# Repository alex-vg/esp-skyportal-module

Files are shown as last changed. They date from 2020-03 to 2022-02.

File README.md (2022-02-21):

## How to make your own ESPSkyPortalModule (a cheap Celestron SkyPortal Wifi-Module alternative)

This little project was inspired by finding a cheaper alternative to the Celestron SkyPortal Wifi Module for NexStar Goto Mounts. With 150€ for such a simple device, it would be crazy not to try and do it ourself. At the end tho, I did not expect that many problems with getting it to communicate correctly, but now it all works fine and I want to share it with you.

If you like this project, you can buy me a beer. Cheers!



### needed stuff:
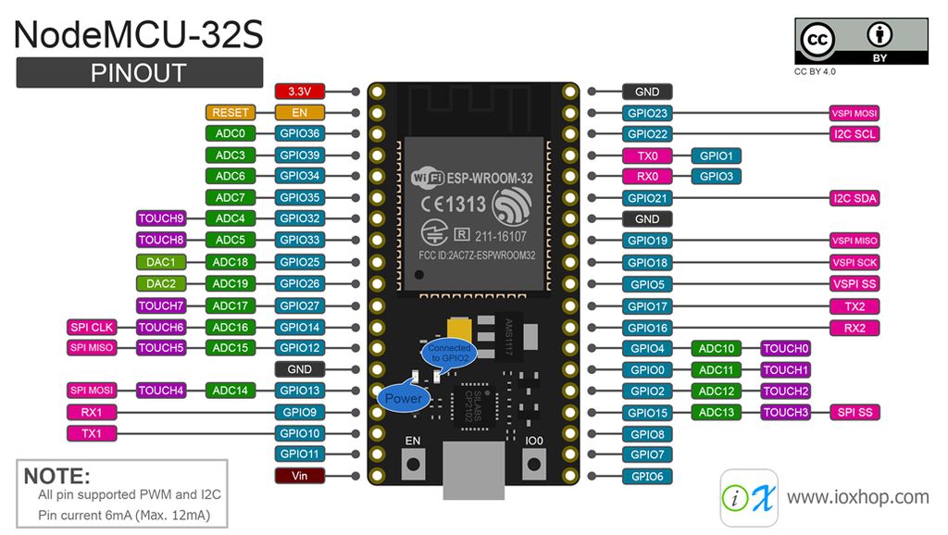
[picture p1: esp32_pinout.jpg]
esp32 pinout

- ESP32, the cheap "NodeMCU32" (see pinout to get the one I used, there are diffrent versions idk if every version works fine)
- 50k-100k resistor (i used exactly 93k ohm, ~2x46k)
- a diode (1N4001, but any other should be ok)
- a small step down converter, to get 5V out of 12V
- RJ12 cable to plug in the device
- (optional) a case or box to protect it

### Pins we need to connect from the 6-pin RJ12 cable:
- PIN3 green - 12V (to step-down module)
- PIN4 yellow - data (to TXPIN, RXPIN and 3.3v)
- PIN5 pink - ground (to every gnd)
- PIN6 gray/black - select (to SELPIN)

Connect the TX pin to the data pin via the diode. TX will just pull the line down, and we need to prevent a high-override. (If Nexstar Device pulls down, this TX output could keep the line high.)
Connect RX Pin directly to the data pin.
```
3.3v --[100k]--+
TXPIN ----<|---+--Data Pin 
RXPIN ---------+
```
Connect a 40k-50k resistor between 3.3v and Data Pin. (a weak pullup, since TX can't pull up anymore and the signal would rise slowly on TX Down -> TX High transition)

Connect the SELPIN directly to the select pin on the RJ12.

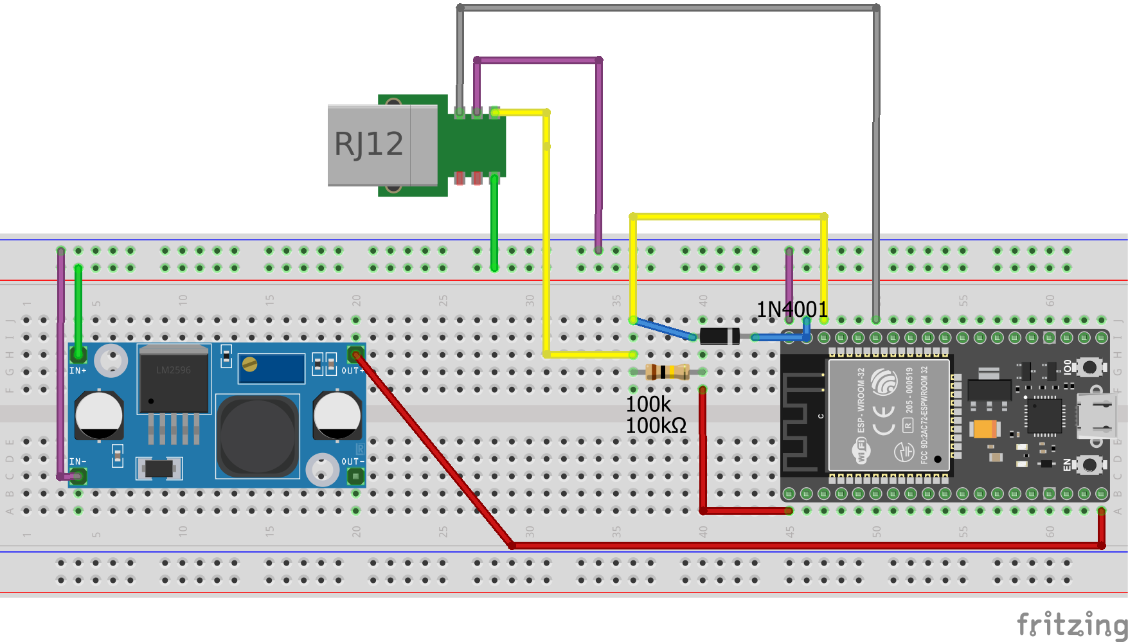
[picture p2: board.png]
board


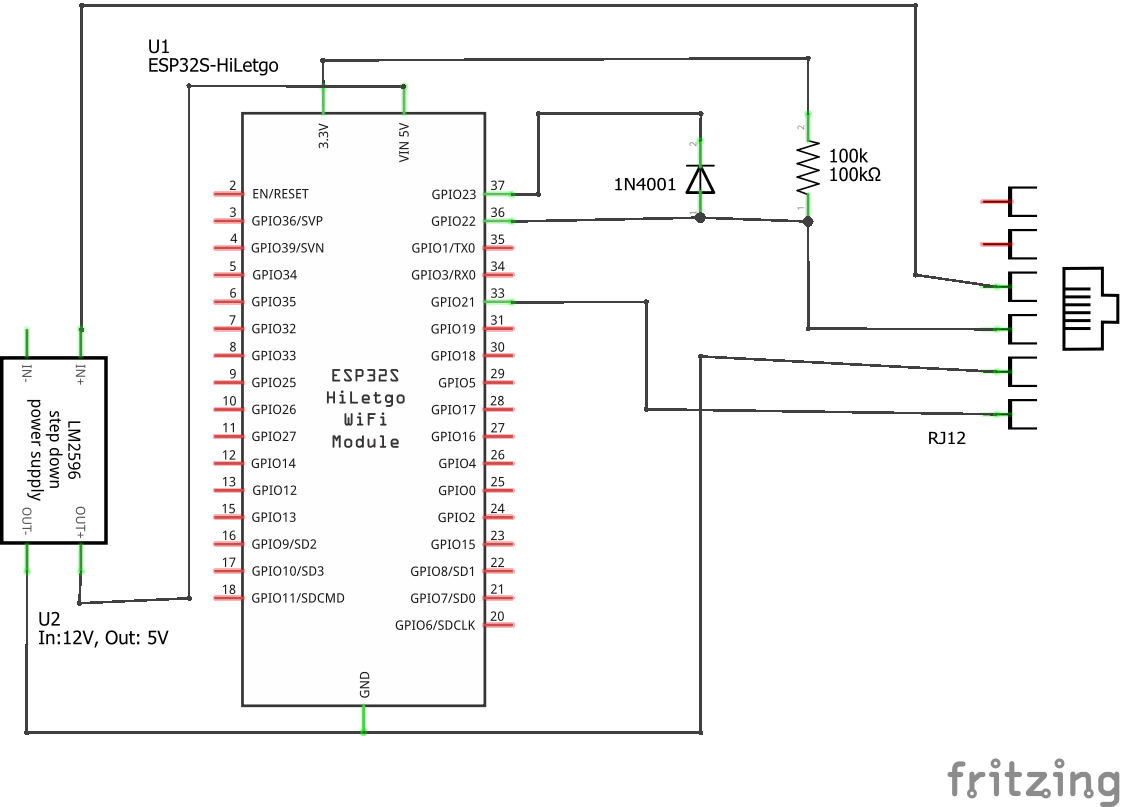
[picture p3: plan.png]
plan


### 5V = 3.3V ?
And yes, we connect our 3.3V IO pins from ESP32 to a potential 5V line. I tried some 3V/5V converters but there are always problems in level shifting.
So the signal from the NexStar is not readable anymore. Then I realized that the Handcontrol is sending at 5V, but the mainboard is responding with a 3.3V level.
The guys from Celestron directly connected 5V and 3.3V logic. Not a good start, but I guessd we could do the same for this project - and it all worked fine.
The only thing that could get grilled is our ESP32, which is cheap.
(But I would still suggest to avoid this in professional product development!)

The device advertises itself via broadcasting its firmware version and mac address.
The control software connects to a tcp port 2000 on ip 1.2.3.4 if the device is in AP mode.
There is a special protocol, but all we need to do is to figure out when a message is complete, since the length of a message can vary. 
After we got a message in the tcp stream, we proxy it to the serial interface and vice versa.

### ToDo-List

- [x] implement Celestron AUX proxy
- [x] implement access-point mode
- [ ] get wifi config with wifi in client-mode working

The original dongle can connect to an existing wifi, after it is configured via the software.
For this connection the software connects to a sort of telnet interface on port 3000.

This is a communication that I sniffed while configuring the original module, to connect to my Wifi with the name Special"Character"WifiName (NX is a message from NexStar, PC is my PC, [0x0d 0x0a] is just a next-line-character):
```
NX:"> "
PC:"get wlan.ssid[0x0d 0x0a]"
NX:Wifiname[0x0d 0x0a]
NX:"> "
...now there are more commands like the one above...
PC:"set wlan.ssid "Special"Character"WifiName"[0x0d 0x0a]"
NX:"Set OK[0x0d 0x0a]"
NX:"> "
...now there are more commands like the one above...
PC:"save[0x0d 0x0a]"
NX:"Success[0x0d 0x0a]"
NX:"> "
```
This is part of ZentriOS (by Silicon Labs) and is indeed a full telnet server with much more functionality.

Commands needed (set and get):

```
set wlan.ssid "ssidname"
set wlan.passkey "mypassword123"
set wlan.static.netmask 0.0.0.0
set wlan.static.ip 0.0.0.0
set wlan.static.gateway 0.0.0.0
set wlan.dhcp.enabled 1
```
Currently I'm not into developing a fake telnet server and since for me there is no need to use an existing wifi, my digitalRead(motivation) returns LOW. But if someone needs this, feel free to contact me.

The ESP32 is available in a "secured" network with the name Celestron-F7F and the password 123456789, which can be changed in the code.

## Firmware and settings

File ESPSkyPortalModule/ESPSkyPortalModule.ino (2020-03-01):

// https://github.com/espressif/arduino-esp32/tree/master/libraries/WiFi/src

//#define DEBUG
//#define DEBUG_INOUT
//#define DEBUG_CRAZY

#include <WiFi.h>
#include <WiFiUdp.h>

#define RXPIN 22
#define TXPIN 23
#define SELPIN 21
#define LEDPIN 2

// Replace with your network credentials
const char* ssid     = "Celestron-F7F";
const char* password = "123456789";

// advertisement over udp. interestingly, the mac advertised starts with 4C, but the actual mac is starting with 4E.
// the end "0F:80" is (0x0F, 0x7F) +1 because WiFi.h uses a diffrent MAC (mac+1) for the server than for wifi advertisment.
const char* advertisment = "{\"mac\":\"4C:55:CC:1A:0F:80\",\"version\":\"ZENTRI-AMW007-1.2.0.10, 2017-07-28T07:43:27Z, ZentriOS-WL-1.2.0.10\"}";

uint8_t mac[] = {0x4E, 0x55, 0xCC, 0x1A, 0x0F, 0x7F};

// tcp 2000
WiFiServer tcpServer(2000);
#define TCPCLIENTMAX 5
WiFiClient tcpClients[TCPCLIENTMAX];
WiFiClient newTcpClient;

// create UDP instance
WiFiUDP udp;

// skyPortal connects to 1.2.3.4:2000
IPAddress local_IP(1, 2, 3, 4);
IPAddress gateway(1, 2, 3, 4);
IPAddress subnet(255, 255, 255, 0);

IPAddress broadcast_IP(255, 255, 255, 255);
uint16_t broadcastToPort=55555;

#define BUFLENGTH 64
char output[BUFLENGTH];

volatile boolean transmission = false;

uint16_t counter = 0;

#define AdLoop 100000
#define LoopTimout 180

void sendAd2() {
    udp.beginPacket(broadcast_IP, broadcastToPort);
    udp.printf("%s", advertisment);
    udp.endPacket();
    #ifdef DEBUG
      Serial.print("-");
    #endif
}

void sendAd() {
    udp.beginPacket(broadcast_IP, broadcastToPort);
    udp.printf("%s", advertisment);
    udp.endPacket();
    #ifdef DEBUG
      Serial.print(".");
    #endif
}

#ifdef DEBUG_INOUT
void debugBufHex(char* buf, unsigned int leng) {
  for(unsigned int i=0; i<leng; i++) {
    if(i==2) {
      Serial.print("[");
    }
    if(buf[i] < 0x10) {
      Serial.print(0, HEX);
    }
    Serial.print(buf[i], HEX);
    if(i==leng-2) {
      Serial.print("]");
    }
    Serial.print(" ");
  }
}

void debugBuf(const char* msg, char *buf) {
  if(msg != NULL) {
    Serial.print(msg);
    Serial.print(" ");
  }
  debugBufHex(buf, BUFLENGTH);
  Serial.print("\n");
}
#endif

void prepareSSWrite() {
  pinMode(TXPIN, OUTPUT);
  digitalWrite(TXPIN, HIGH);
}

void prepareSSRead() {
  pinMode(RXPIN, INPUT_PULLUP);
}

void WiFiEventConfigureWifi(WiFiEvent_t event, WiFiEventInfo_t info) {
  // configure...
  #ifdef DEBUG
    Serial.println(WiFi.softAPConfig(local_IP, gateway, subnet) ? "Configured" : "Failed to configure!");
  #else
    WiFi.softAPConfig(local_IP, gateway, subnet);
  #endif
  IPAddress IP = WiFi.softAPIP();
  #ifdef DEBUG
    Serial.print("AP IP address: ");
    Serial.println(IP);
  #endif
}

bool waitForSelect(unsigned long timeout) {
  unsigned long startMillis = millis();
  while(digitalRead(SELPIN)==LOW && millis() - startMillis < timeout);
  return (digitalRead(SELPIN)==HIGH);
}

size_t readAnyStream(Stream *inputStream, const char* descr, char* buffer) {
  size_t leng;
  size_t totalLeng;
  size_t readLeng;
  inputStream->setTimeout(15);
  if(inputStream->find(0x3B)) { // timeout returns false after Serial2.setTimout..
    leng = inputStream->read();
    totalLeng = leng+3;
    buffer[0]=0x3B;
    buffer[1]=leng;
    readLeng = inputStream->readBytes(&buffer[2], leng+1);
    if(readLeng != leng+1) {
      #ifdef DEBUG
        Serial.print(descr);
        Serial.print(" got ");
        Serial.print(readLeng);
        Serial.print(" but expected ");
        Serial.print(leng+1);
        Serial.println(" bytes. (timeout)");
      #endif
    }
    return readLeng+2;
  }
  return 0;
}

void writeAllStreams(WiFiClient outputStreams[], size_t streamsSize, size_t leng, const char* descr, char* buffer) {
  for(size_t i=0; i<streamsSize; i++) {
    if (!outputStreams[i].connected()) {
      continue;
    }
    char *desc2 = (char*)malloc(sizeof(descr)+4);
    sprintf(desc2,"%s(%i)",descr,i);
    writeAnyStream(&outputStreams[i], leng, desc2, buffer);
  }
}

void writeAnyStream(Stream *outputStream, size_t leng, const char* descr, char* buffer) {
  outputStream->write(buffer, leng);
  #ifdef DEBUG_INOUT
    Serial.print(descr);
    Serial.print(" (");
    Serial.print(leng);
    Serial.print("): ");
    debugBufHex(buffer, leng);
    Serial.println("");
  #endif
}

void serialEvent2(WiFiClient tcpClients[]) {
  size_t leng = readAnyStream(&Serial2, "from NS ", output);
  if (leng > 2 && output[2] == 0x20) {
    #ifdef DEBUG_INOUT
      Serial.print("from NS detected echo. ");
      debugBufHex(output, leng);
      Serial.println("");
    #endif
    serialEvent2(tcpClients);
    return;
  }
  if(leng > 0) {
    writeAllStreams(tcpClients, TCPCLIENTMAX, leng, "from NS ", output);
  }
}

void tcpEvent(WiFiClient *tcpClient) {
  size_t leng = readAnyStream(tcpClient, "from TCP", output);
  if(leng > 0) {
    if(!waitForSelect(600)) {
      // can't write... NS is busy
      return;
    }
    setSelOutput();
    delayMicroseconds(400);
    writeAnyStream(&Serial2, leng, "from TCP", output);
    delayMicroseconds(400);
    Serial2.flush();
    setSelInput();
  }
}

void serial_ISR() {
  transmission = true;
}

void setSelOutput() {
  detachInterrupt(digitalPinToInterrupt(SELPIN));
  pinMode(SELPIN, OUTPUT);
  digitalWrite(SELPIN, LOW);
}

void setSelInput() {
  pinMode(SELPIN, INPUT_PULLUP);
  attachInterrupt(digitalPinToInterrupt(SELPIN), serial_ISR, FALLING);
}

void setup() {
  esp_base_mac_addr_set(&mac[0]);
  Serial.begin(115200);
  Serial2.setTimeout(1000);
  tcpServer.setTimeout(1000);

  // Connect to Wi-Fi network with SSID and password
  Serial.println("Setting AP (Access Point)...");

  WiFi.onEvent(WiFiEventConfigureWifi, WiFiEvent_t::SYSTEM_EVENT_AP_START);

  // Add the password parameter, if you want the AP (Access Point) to be open
  // WiFi.softAP(ssid, password);
  WiFi.softAP(ssid, password);
  Serial.print("WiFi Mac: ");
  Serial.println(WiFi.macAddress());

  tcpServer.begin();
  tcpServer.setNoDelay(true);
  //tcpServer.setTimeout(5);

  Serial2.begin(19200, SERIAL_8N2, RXPIN, TXPIN);
  prepareSSWrite();
  prepareSSRead();
  setSelInput();
}

void loop(){
  counter++;
  if (counter % AdLoop == 0) {
    sendAd2();
  }

  newTcpClient = tcpServer.available();


  if(newTcpClient) {
    for(uint8_t i=0; i<TCPCLIENTMAX; i++) {
      if(!tcpClients[i].connected()) {
        tcpClients[i] = newTcpClient;
        #ifdef DEBUG
          Serial.print("Connect on 2000! (");
          Serial.print(i);
          Serial.println(")");
        #endif
        break;
      }
    }
  }
  

  for(uint8_t i=0; i<TCPCLIENTMAX; i++) {                             // If a new client connects,
    if(!tcpClients[i].connected()) {
      continue;
    }

    if (tcpClients[i].connected()) {

      if (tcpClients[i].available()) {             // if there's bytes to read from the client,
        tcpEvent(&tcpClients[i]);
      }

      if(Serial2.available() || transmission) {
        noInterrupts();
        transmission = false;
        serialEvent2(tcpClients);
        interrupts();
      }
    } else {
      // Close the connection
      tcpClients[i].stop();
  
      #ifdef DEBUG
        Serial.print("Connection lost. (");
        Serial.print(i);
        Serial.println(")");
      #endif
    }
  }
}
